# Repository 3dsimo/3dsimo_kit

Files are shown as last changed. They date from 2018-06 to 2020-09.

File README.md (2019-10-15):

# 3Dsimo KIT information

## Watch our PROMO video for 3Dsimo KIT 2 product

Visit us at [3D simo pages](https://3dsimo.com/) for more information

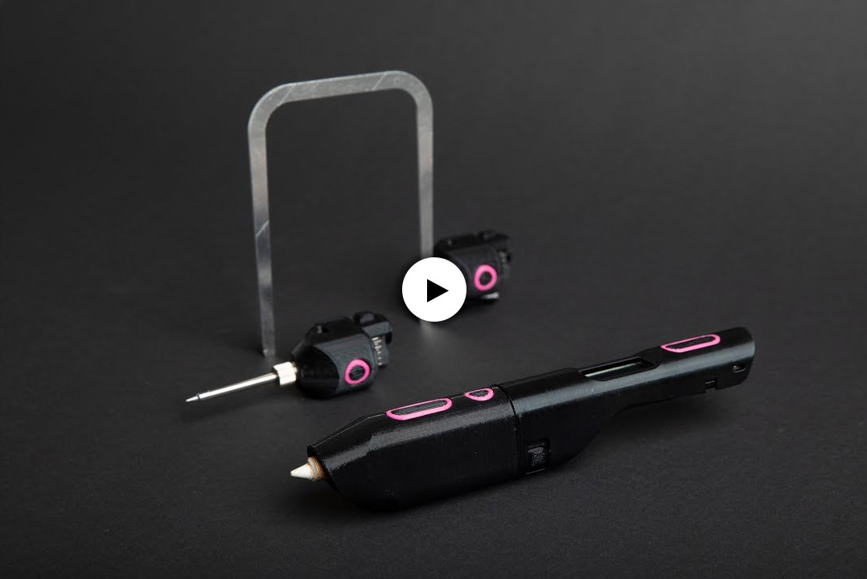
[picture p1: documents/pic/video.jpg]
(https://www.youtube.com/watch?v=d5TUmM0rqjs)


## [3D printed parts](documents/3Dprint.md)
This section includes information about all 3D printed plastic parts. Folder [3Dmodels](3Dmodels) includes all parts in STP and STL formats for both version of 3Dsimo KIT. You can download it and edited it as you want. If your models will be awsome, we can publish them here.

## [Hardware for 3Dsimo KIT](documents/Hardware.md)
Electronics device is an essential part of the 3Dsimo KIT. Main board is a "heart" of the device and manage all functions such as heating, identification or extrusion. 

## [Firmware for 3Dsimo KIT](documents/Firmware.md)
Microcontroller requries a program which can run the device. 3Dsimo KIT has code written in C/C++ language in [Arduino IDE](https://www.arduino.cc/) and it is easy to edit.

## [Arduino nano](documents/ArduinoNano.md)
Information about Arduino Nano like development board. 

## [Manuals](documents/Manual.md)
Manual for device operations and how to edit your Arduino Nano like development kit for 3Dsimo KIT. 

<!--
## [Material profiles](documents/MaterialProfiles.md)
-->

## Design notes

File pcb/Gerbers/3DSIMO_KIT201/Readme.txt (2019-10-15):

I order Rigid Board with these parameters and files:

Name:               3DSIMO_KIT201
Customer:           3DSimo

PCB Parameters:
Type:               Rigid FR4
Number of layers:   2 rigid 
Final thickness:    1.6 mm
Copper thickness:   35um
Coating:            HAL Free
Soldermask TOP:		Black
Soldermask BOT:		Black
Silkscreen TOP:		White
Silkscreen Bottom:  White
Dimensions:			17 x 85 mm

Input Files:
bot.gbr             Copper - BOTTOM side
top.gbr             Copper - TOP side   
mill.gbr            Milling of PCB
plt.gbr             Silkscreen - TOP
plb.gbr             Silkscreen - BOTTOM
smb.gbr             Solder mask - BOTTOM side
smt.gbr             Solder mask - TOP side
npth.exc            Non plated drills
pth.exc             Plated drills
paste_top.gbr       SMD stencil - TOP

Copper order:
TOP
BOTTOM

Output testing:
Electrical testing: YES

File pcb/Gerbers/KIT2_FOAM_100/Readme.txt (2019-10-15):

I order Rigid Board with these parameters and files:

Name:               KIT2_FOAM_100
Customer:           3DSimo

PCB Parameters:
Type:               FR4
Number of layers:   2 
Final thickness:    1.6 mm
Copper thickness:   35um
Coating:            Immersion Au
Soldermask TOP:		White
Soldermask BOT:		White
Silkscreen TOP:		None
Silkscreen Bottom:  None
Board dimensions:	26.30 x 17.15 mm

Input Files:
bot.gbr             Copper - BOTTOM side 
top.gbr             Copper - TOP side    
mill.gbr            Milling of PCB
smb.gbr             Solder mask - BOTTOM side
smt.gbr             Solder mask - TOP side
npth.exc            Non plated drills
pth.exc             Plated drills  
paste_top.gbr		Stencil layer TOP

Copper order:
TOP
BOTTOM 

Output testing:
Electrical testing: YES

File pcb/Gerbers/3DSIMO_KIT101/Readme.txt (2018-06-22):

I order Rigid Board with these parameters and files:

Name:               3DSIMO_KIT101
Customer:           3DSimo

PCB Parameters:
Type:               Rigid FR4
Number of layers:   2 rigid 
Final thickness:    1.6 mm
Copper thickness:   35um
Coating:            HAL Free

Input Files:
bot.gbr             Copper - BOTTOM side
top.gbr             Copper - TOP side   
mill.gbr            Milling of PCB
plb.gbr             Silkscreen - BOTTOM
plt.gbr             Silkscreen - TOP
smb.gbr             Solder mask - BOTTOM side
smt.gbr             Solder mask - TOP side
npth.exc            Non plated drills
pth.exc             Plated drills

Copper order:
TOP
BOTTOM

Output testing:
Electrical testing: YES

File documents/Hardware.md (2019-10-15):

# Hardware for 3Dsimo KIT 2

3Dsimo KIT 2 is based on standard Arduino Nano platform with modified layout designed especially for 3D pen with interchangable extensions. Its simplified design lead to smaller footprint and thus smaller and more ergonomical design of the whole device. 

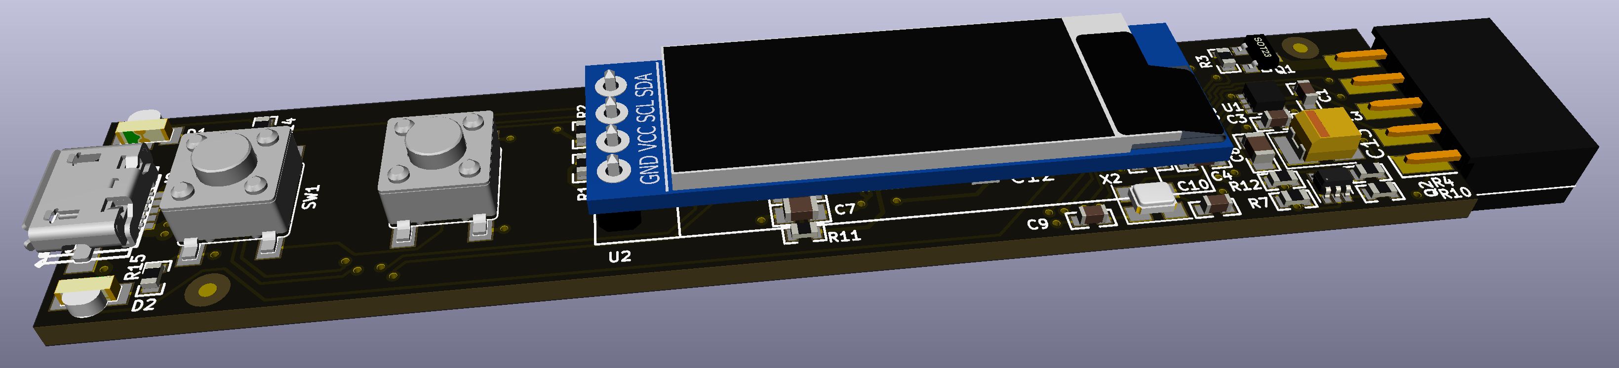
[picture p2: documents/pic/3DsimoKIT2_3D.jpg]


### Power
The pen runs at 5V power through micro USB connector which is possible to use as a programming interface as well. The device requires power adapter with at least 2A and 5V. 

### Display
OLED display based on SSD1306 driver is connected through an TWI interface to the microcontroller. There are two external pull-ups resistor which are making logical 1 for the TWI bus and no additional components are required.

### Programming interface
The microcontroller is possible to reprogram through the USB and USB<>UART converter. The layout is similar to standard Arduino Nano programming interface, but chosen converter is different - CP2102N. Program is written in C/C++ language in Arduino IDE. More information about programming you can find in [Firmware chapter](Firmware.md).

### Layout
3Dsimo KIT 2 contains 4 boards, where one is main board with MCU and three boards are used for interchangable extensions. All boards are designed in Open-source program [KiCAD](http://kicad-pcb.org/) in the recent version 5.1.4. 3D models are mainly taken from KiCADs repositories, but several were drawn or taken from the manufacturer and they are not included in KiCADs github. You can find them in folder with all [3D models](../pcb/Documents/3D) used for 3DSimo KIT.

### Temperature measurement
3Dsimo KIT2 is equipped with two ranges thermal measurement, one for PCL materials (temperatures in range from 30°C to 120°C) and the second one for other plastics material such as ABS, PLA, etc. (from 180°C to 300°C). These two ranges provides unlimited possibilities in different material usage. 

### Schematics and Assembling
Schematics of the 3Dsimo KIT 2 is possible to download at [following link](../pcb/Documents/3DsimoKit201_Schematics.pdf)

Assembling and components placement can be downloaded at [following link](../pcb/Documents/3DsimoKit201_AssemblyTop.pdf)

# Hardware for 3Dsimo Kit
3Dsimo KIT is developed on Arduino Nano like development board with additional interface board containing motor driver and OLED display. 

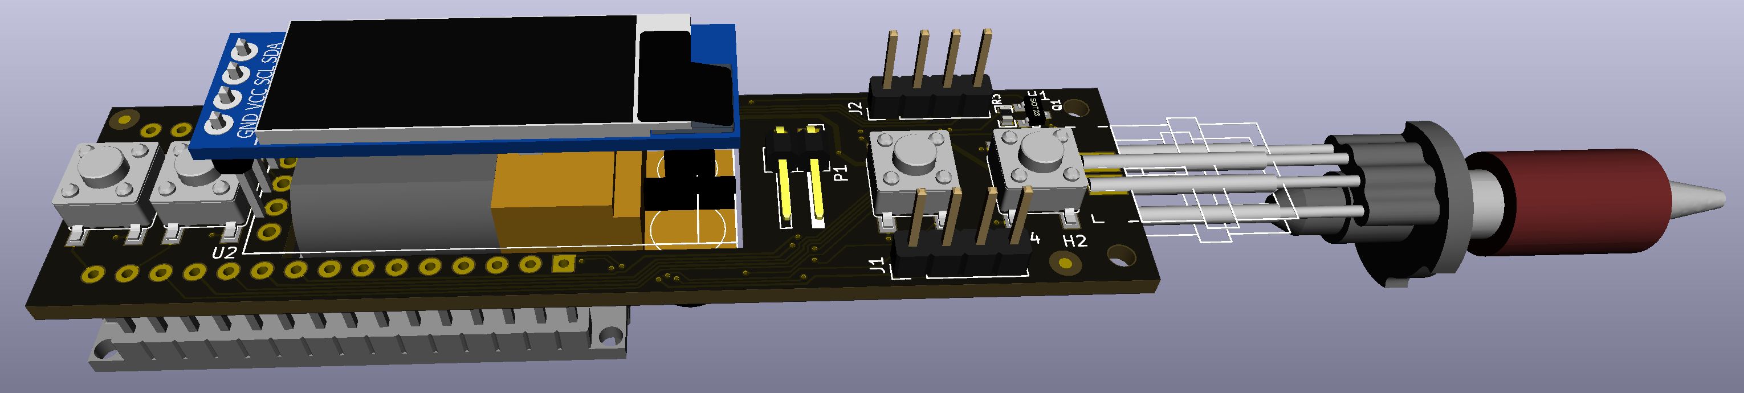
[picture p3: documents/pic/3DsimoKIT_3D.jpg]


### Power
The pen runs at 5V power through mini USB connector located on Arduino Nano like board. The development board requires one modification, replace input protection diode for shortcut. 3Dsimo KIT requires power adapter with at least 2A and 5V. 

### Display
OLED display based on SSD1306 driver is connected through an TWI interface and additional board to the microcontroller. There are two external pull-ups resistor which are making logical 1 for the TWI bus and no additional components are required.

### Programming interface
The microcontroller is possible to reprogram through the mini USB connector placed directly on the Arduino Nano like development kit. Program is written in C/C++ language in Arduino IDE. More information about programming you can find in [Firmware chapter](Firmware.md).

### Layout
3Dsimo KIT contains one interface board, which is used for connecting display, buttons, motor driver and etc. with MCU. The board is designed in Open-source program [KiCAD](http://kicad-pcb.org/). 3D models are mainly taken from KiCADs repositories, but several were drawn or taken from the manufacturer and they are not included in KiCADs github. You can find them in folder with all [3D models](../pcb/Documents/3D) used for 3DSimo KIT.

### Temperature measurement
3Dsimo KIT is equipped with only one range for melting common plastics for 3D printers such as ABS, PLA, etc. and its range is from 180°C to 300°C. 

### Schematics and Assembling
Schematics of the 3Dsimo KIT 2 is possible to download at [following link](../pcb/Documents/3DsimoKit101_Schematics.pdf)

Assembling and components placement can be downloaded at the following links [TOP](../pcb/Documents/3DsimoKit101_AssemblyTop.pdf) and [BOTTOM](../pcb/Documents/3DsimoKit101_AssemblyBottom.pdf)

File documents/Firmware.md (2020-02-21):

# Firmware for 3Dsimo KIT
If you want to learn how the pen works or you want to add your own material profiles, or you want to make some changes and tweaks, you are on the right address. The code is fully available and commented so you don't have trouble finding your way around. For both versions of the 3Dsimo KIT Firmwares are inside folders [FW](../FW). 

Microcontroller is programmed in C/C++ language in the editor [Arduino IDE](https://www.arduino.cc/). 

Main code is divided into several files, where every have different purpose. Following listing explains their purpose:
 - **config.h** is for setting pins and general settings of the board 
 - **accessories.c/.h** contains functions for every extension
 - **NanodeUNIO.c/.h** is library for one wire UNI/O protocol, it is used for identification the extensions

Before you start to program or edit the code, it is required to download some libraries listed below.

## Libraries to download
Code for 3Dsimo KIT requires following two libraries which have to be downloaded. 
 - **EveryTimer** by *Alessio Leoncini*
 - **ssd1306** by *Alexey Dynda*
 
Both libraries you can download directly from Arduino IDE according to following image (Sketch -> Include Library -> Manage Libraries ...)

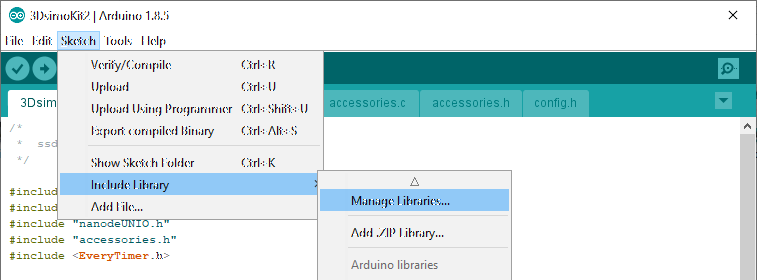
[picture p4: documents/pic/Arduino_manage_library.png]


## Setting up Arduino IDE
### Board
Both version of the 3Dsimo KIT requires to choose development kit Arduino Nano board (Tools -> Board: ... -> Arduino Nano)

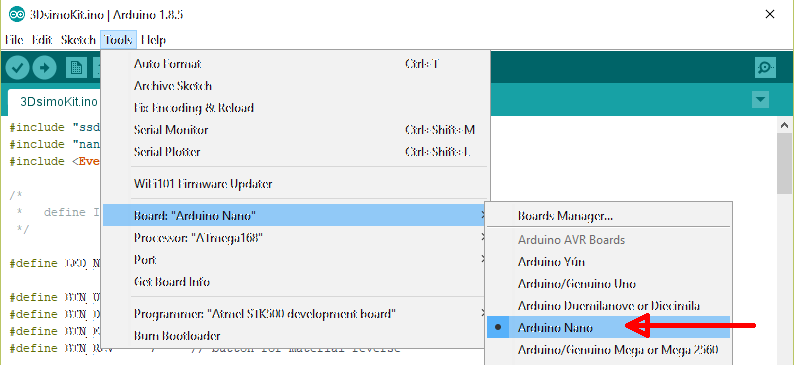
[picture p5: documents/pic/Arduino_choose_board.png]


### COM port
Select port where is connected your development kit (Tools -> Port -> COMxx). In the image, there is selected COM3, but your board can be connected to a different one.

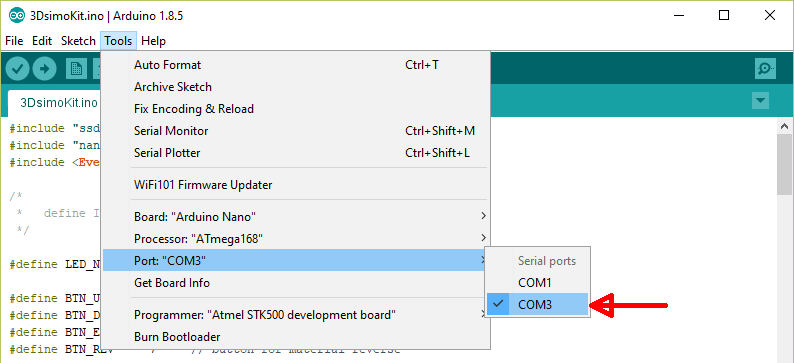
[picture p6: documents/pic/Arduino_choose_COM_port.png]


### Processor
**3Dsimo KIT** can use both types of microcontroller, you have to check it which one you have. The most probably version is **ATmega168**. 

The **3Dsimo KIT 2** is using **ATmega328P**. 

Please be sure, you are using the right version of the bootloader. Arduino released a new version of Arduino IDE, where updated bootloader for Arduino NANO boards. In this case, used setting with a processor called **ATmega328P (old bootloader)**. 

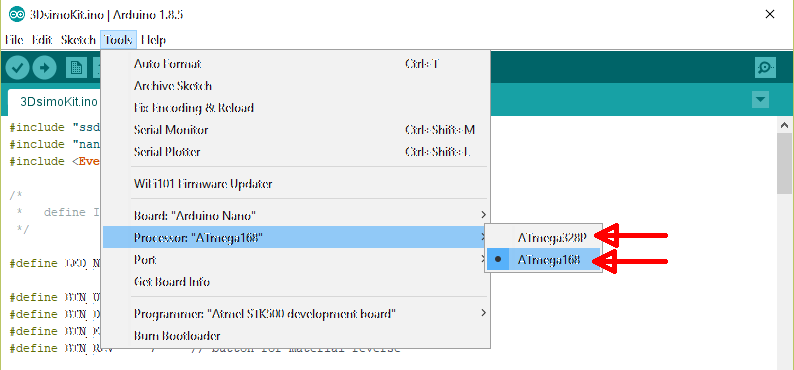
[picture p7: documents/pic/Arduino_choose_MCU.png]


## Compiling and uploading code

When you finish editing your code, it is possible to verify it by the first button "Verify" (1) and in case of no errors upload it to the microcontroller by the second (2) button "Upload". Uploading progress bar will indicate the process of the upload. When code is successfully uploaded into microcontroller, the status will be following: "Done uploading".

In case of error, the editor will not permit to upload the code into microcontroller.

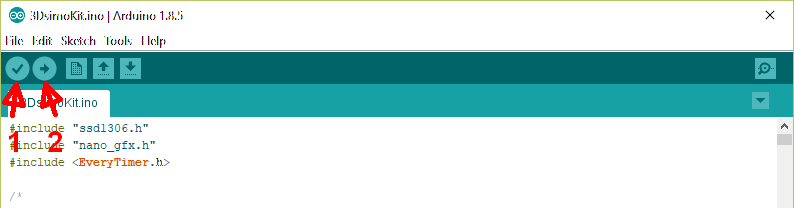
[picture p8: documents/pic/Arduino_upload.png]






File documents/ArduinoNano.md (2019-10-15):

# Arduino Nano development kit
3Dsimo KIT is based on very popular Arduino Nano. It is very likely that you already come across it but in case you haven't yet here are some things you might find useful.

The first version of 3Dsimo KIT requires standard Arduino Nano board, but it is necessary to perform one small improvement (development boards supplied by 3Dsimo have this improvement performed). It is necessary to replace input protection diode which limits input power to the board. The 3D extension requires more than 1.5A and this diode limit the current to approx 500mA. It depends on type. Replacement is illustrated in the following image in red circle. There is replaced diode by 0R resistor.

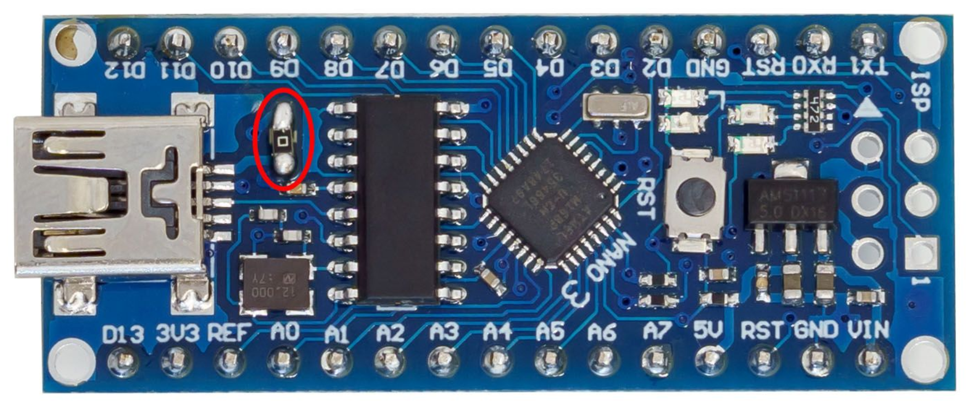
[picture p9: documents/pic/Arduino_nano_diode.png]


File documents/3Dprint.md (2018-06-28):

# 3D print
Plastic parts of 3Dsimo KIT are printed on FDM printers and can be easily swapped. We intend to add new parts and new designs all the time. All 3D models are of course available, so you can modify them as you please. IF you have an interesting model don't hesitate to share it with us.

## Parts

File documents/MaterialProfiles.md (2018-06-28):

# Material profiles
3Dsimo KIT already contains profiles for ABS and PLA of the box, but thanks to its nature, it can handle other materials easily as well. You can even add them yourself by changing our available code and adding your own material profiles.

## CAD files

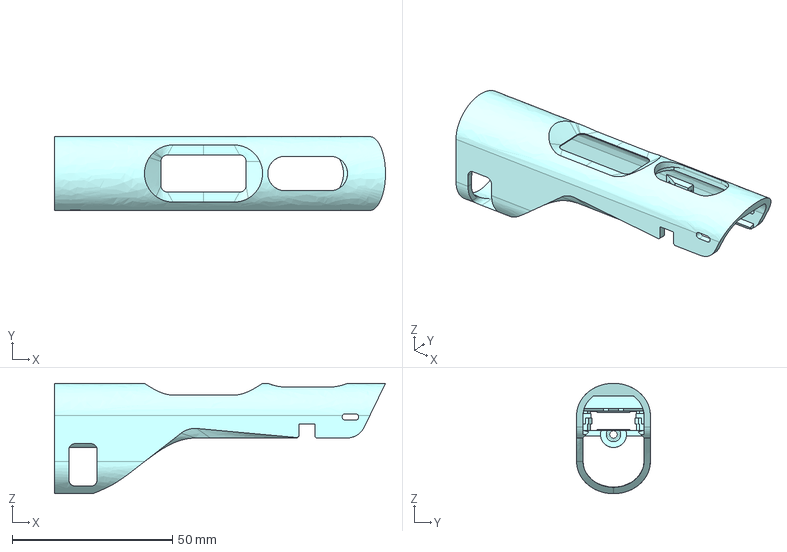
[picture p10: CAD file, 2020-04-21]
3Dmodels/3Dsimo KIT2/Newer/STP/MAIN BODY.step
103.1 x 23.0 x 34.4 mm

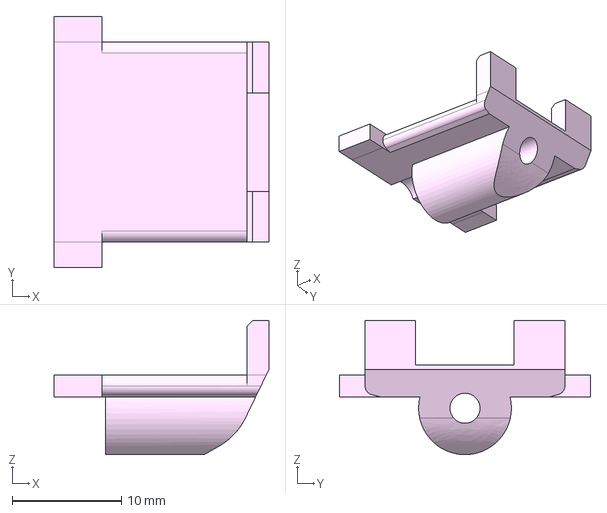
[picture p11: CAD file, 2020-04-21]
3Dmodels/3Dsimo KIT2/Newer/STP/MAIN_PCB_FASTENING v1.step
19.7 x 23.0 x 12.3 mm

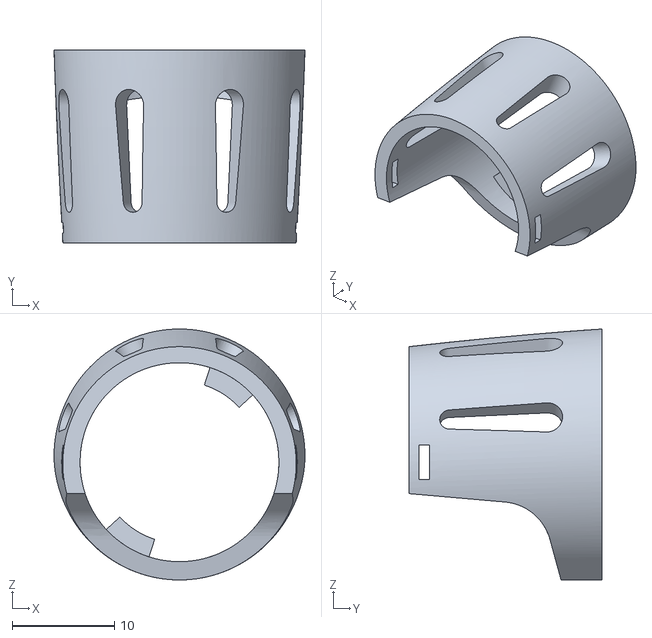
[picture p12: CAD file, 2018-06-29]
3Dmodels/3Dsimo KIT/original/STL/Front_Ring_Alt_1.stl
24.5 x 18.8 x 24.5

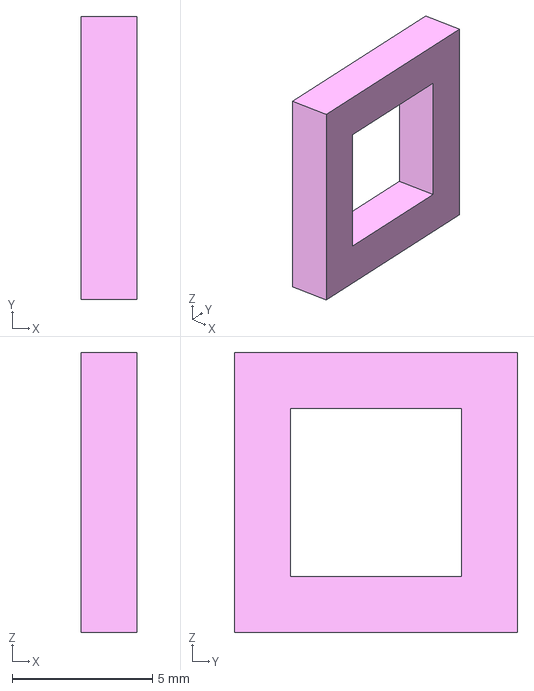
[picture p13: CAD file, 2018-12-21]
3Dmodels/3Dsimo KIT/original/STP/Lock_side_2x.stp
2.00 x 10.1 x 10.0 mm

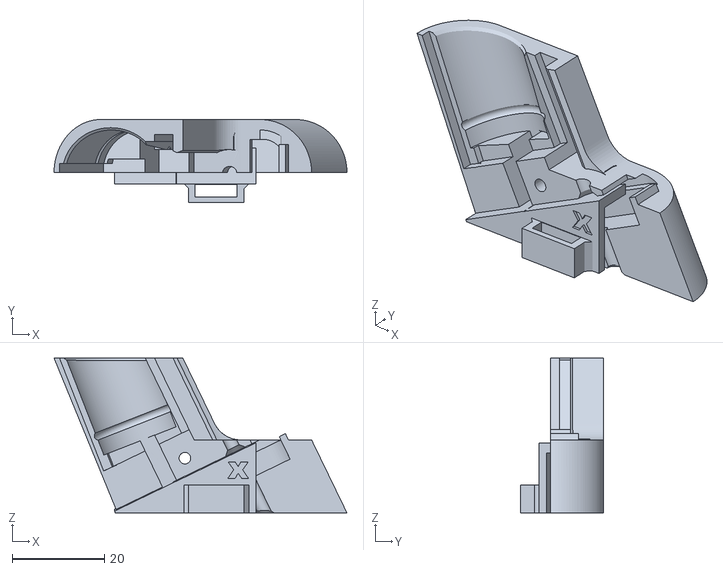
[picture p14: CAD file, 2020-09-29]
3Dmodels/3Dsimo KIT2/Battery_adaptor/modeled supports/BAT_LEFT_SUPPORTS.stl
63.4 x 17.9 x 33.5

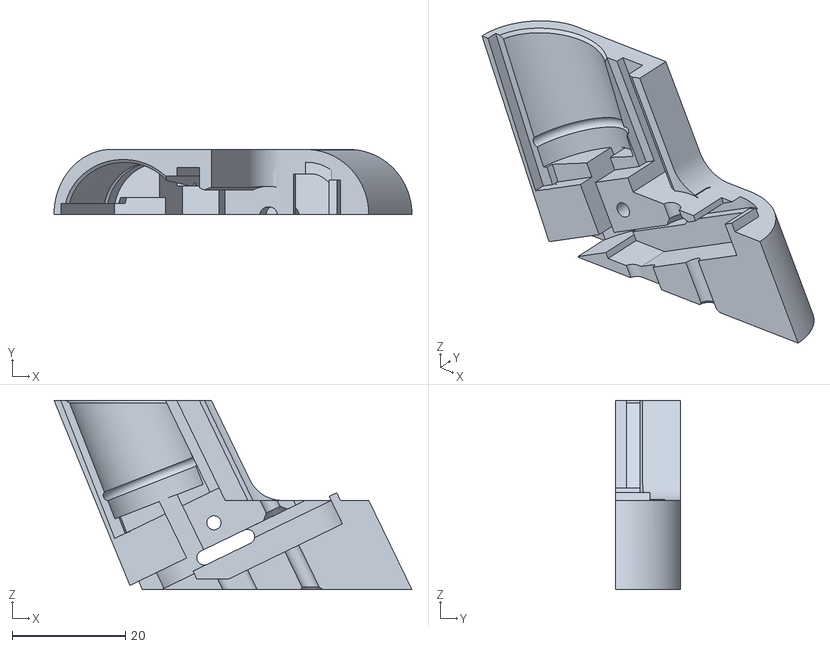
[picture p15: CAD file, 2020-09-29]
3Dmodels/3Dsimo KIT2/Battery_adaptor/original/BAT_LEFT.stl
63.4 x 11.5 x 33.5

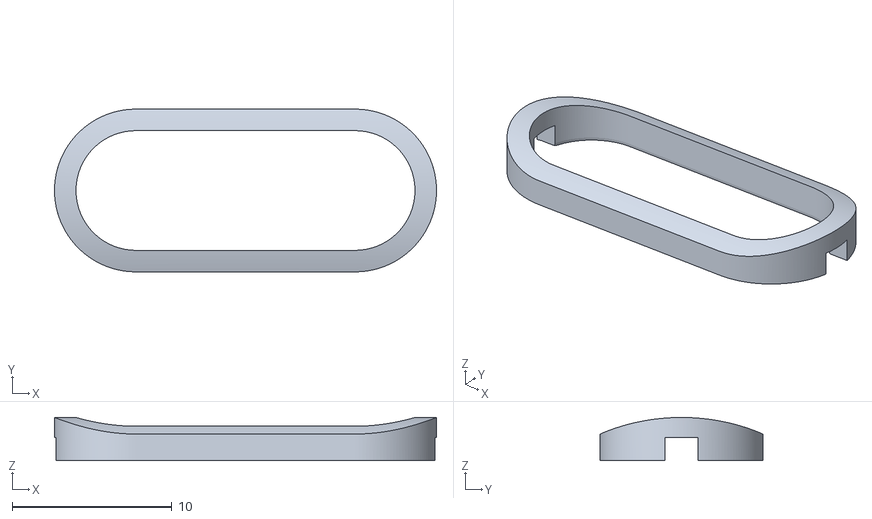
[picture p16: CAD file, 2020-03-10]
3Dmodels/3Dsimo KIT2/Newer/STL/DOUBLE BUTTON RING.stl
23.9 x 10.2 x 2.70

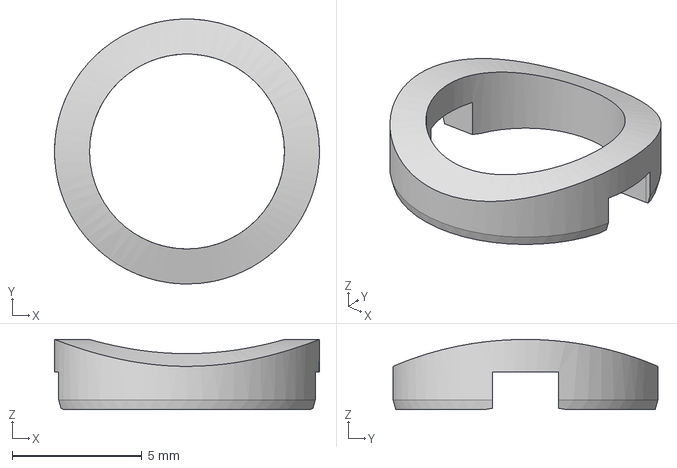
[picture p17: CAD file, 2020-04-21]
3Dmodels/3Dsimo KIT2/Newer/STP/SINGLE_BUTTON_RING v1.step
10.2 x 10.2 x 2.70 mm

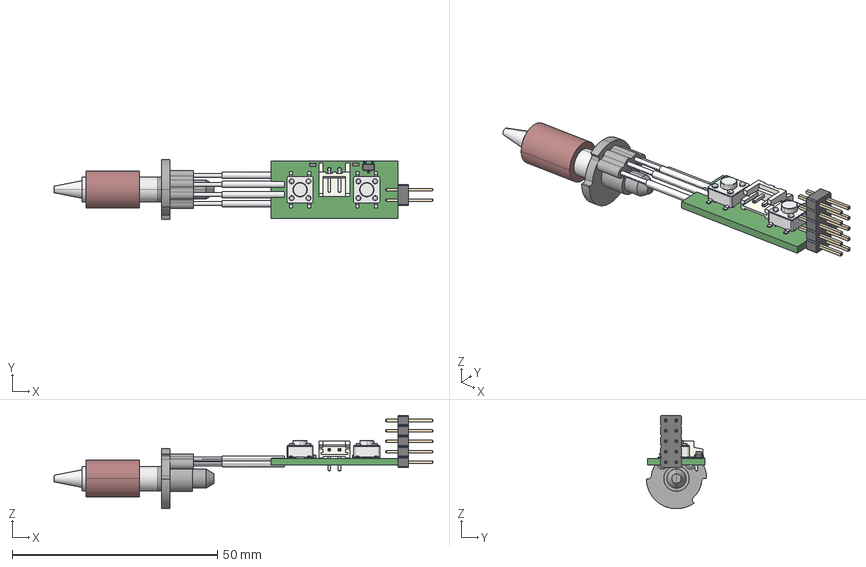
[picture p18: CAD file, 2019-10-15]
pcb/Documents/3D/KIT2_3D_extension100.step
92.4 x 14.7 x 22.8 mm

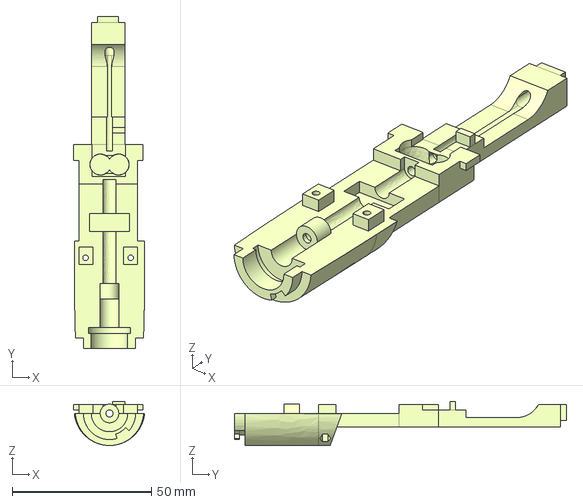
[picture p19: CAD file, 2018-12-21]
3Dmodels/3Dsimo KIT/original/STP/Central_bottom.stp
25.6 x 119.1 x 15.8 mm

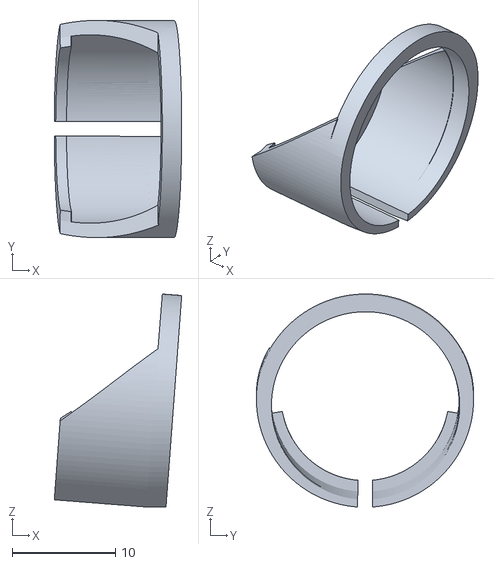
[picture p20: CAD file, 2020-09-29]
3Dmodels/3Dsimo KIT2/Battery_adaptor/original/BAT_RING.stl
12.3 x 21.0 x 20.6

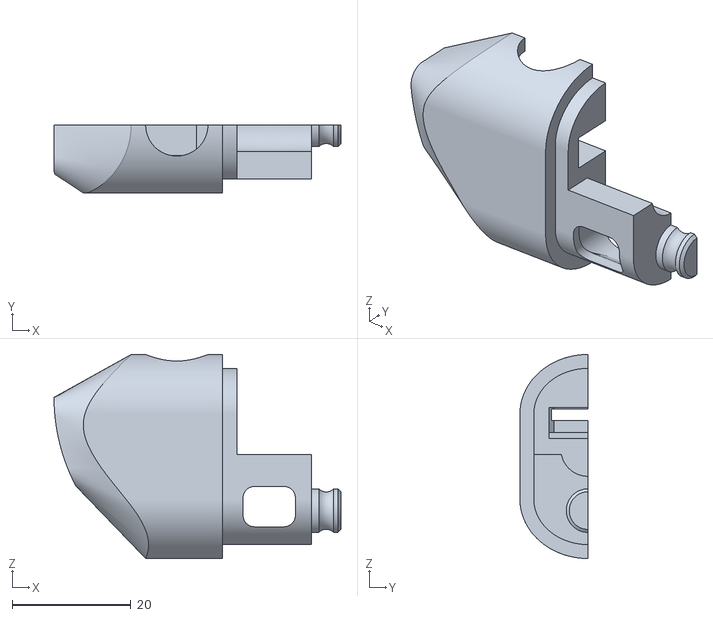
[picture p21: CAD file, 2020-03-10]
3Dmodels/3Dsimo KIT2/Newer/STL/FOAM LEFT.stl
48.4 x 11.5 x 34.4

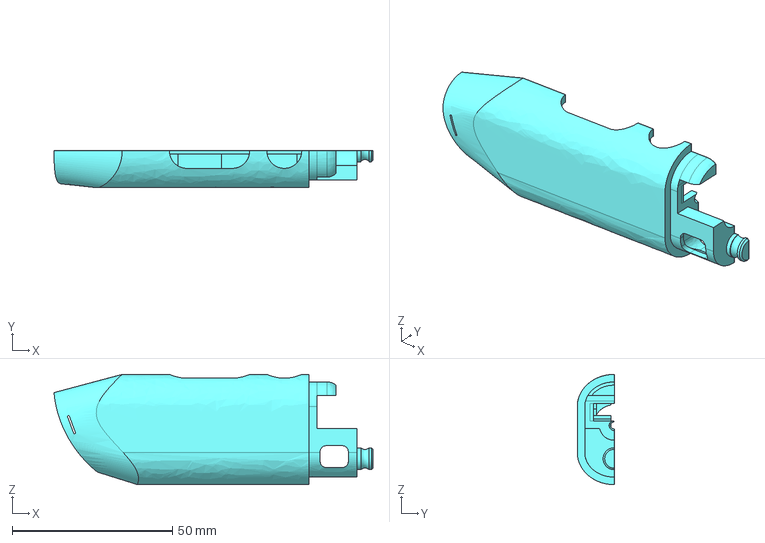
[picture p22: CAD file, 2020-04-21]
3Dmodels/3Dsimo KIT2/Newer/STP/3D_DRAW_R.step
99.6 x 11.7 x 34.4 mm

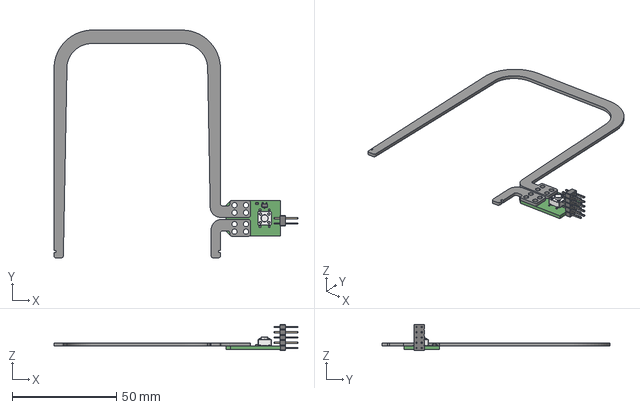
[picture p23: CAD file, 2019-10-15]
pcb/Documents/3D/KIT2_foam_cutting100.step
117.3 x 109.5 x 12.7 mm

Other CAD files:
3Dmodels/3Dsimo KIT2/Battery_adaptor/modeled supports/BAT_RIGHT_SUPPORTS.stl
3Dmodels/3Dsimo KIT/original/STP/Central_top.stp
3Dmodels/3Dsimo KIT2/Battery_adaptor/modeled supports/BAT_RING_SUPPORTS.stl
3Dmodels/3Dsimo KIT2/Battery_adaptor/original/BAT_RIGHT.stl
3Dmodels/3Dsimo KIT/original/STL/Back_Top.stl
3Dmodels/3Dsimo KIT/original/STL/Central_Bottom.stl
3Dmodels/3Dsimo KIT/original/STL/Central_Top.stl
3Dmodels/3Dsimo KIT/original/STL/Front_Ring.stl
3Dmodels/3Dsimo KIT/original/STL/Front_Ring_Alt_2.stl
3Dmodels/3Dsimo KIT/original/STL/Lock_Back.stl
3Dmodels/3Dsimo KIT/original/STL/Lock_Side_2x.stl
3Dmodels/3Dsimo KIT/original/STL/Tube_Holder.stl
3Dmodels/3Dsimo KIT/original/STP/Back_top.stp
3Dmodels/3Dsimo KIT/original/STP/Front_ring.stp
3Dmodels/3Dsimo KIT/original/STP/Front_ring_Alt_2.stp
3Dmodels/3Dsimo KIT/original/STP/Lock_back.stp
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

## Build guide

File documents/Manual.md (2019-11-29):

# 3Dsimo KIT manuals
Want to learn more about 3Dsimo KIT? Everything you should know about it can be find here. Steps how to assemble the pen, how to power it, how to program it, what types of filament to use.

## English Manual

[Assembly Manual 3Dsimo KIT](pdf/manualEN.pdf)

[Assembly Manual 3Dsimo KIT2](pdf/KIT_2_4in1_en.pdf)

## Czech Manual

[Assembly Manual 3Dsimo KIT](pdf/manualCZ.pdf)

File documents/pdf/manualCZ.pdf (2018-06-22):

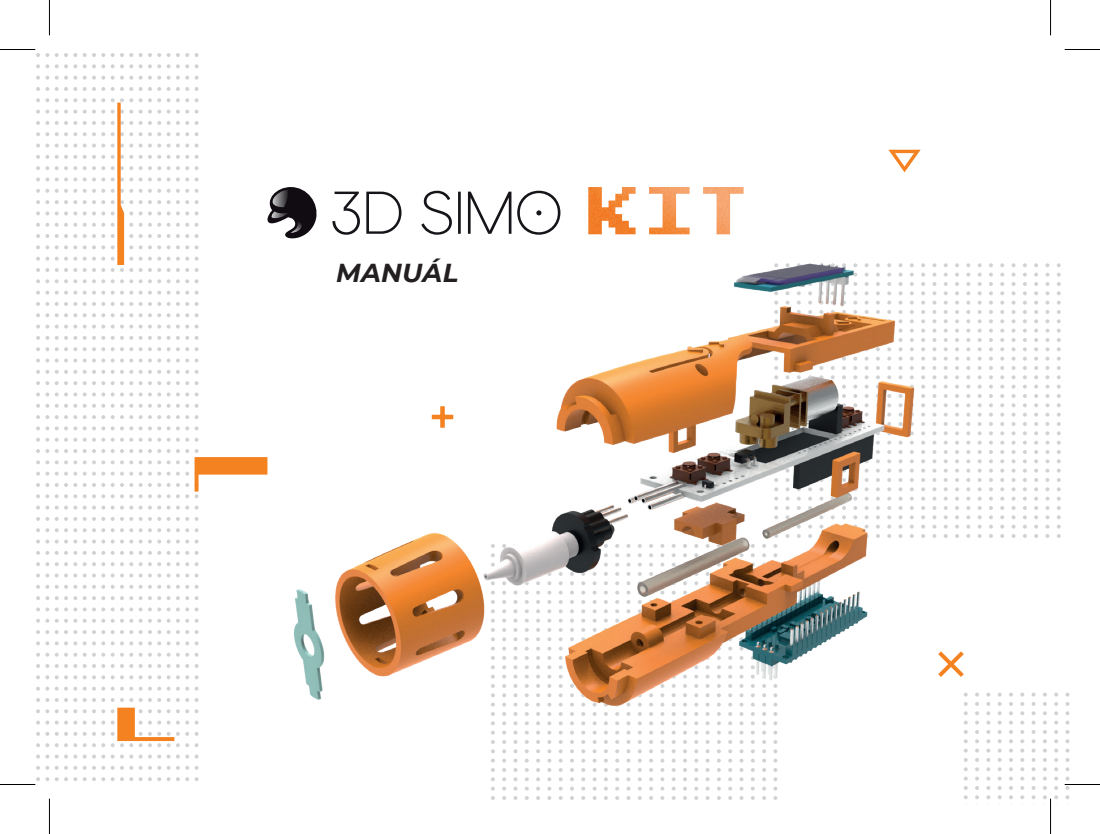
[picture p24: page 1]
MANUÁL

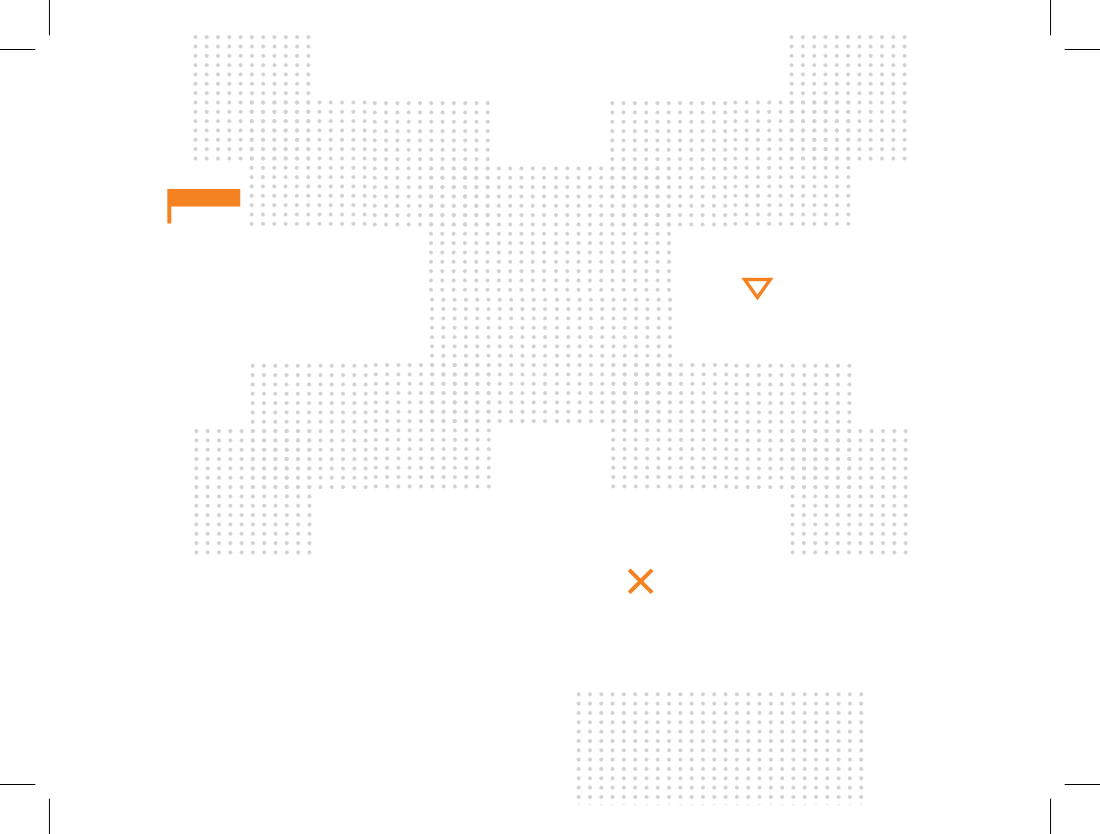
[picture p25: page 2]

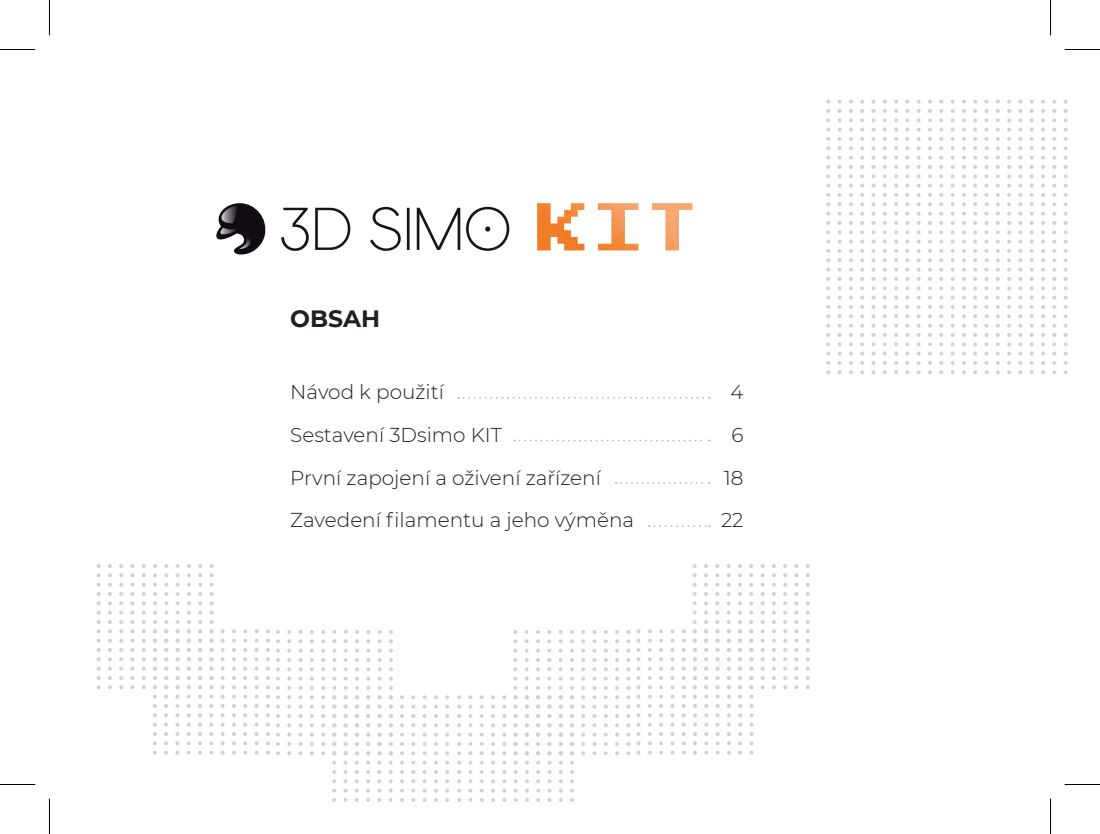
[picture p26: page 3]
OBSAH

Návod k použití
Sestavení 3Dsimo KIT
První zapojení a oživení zařízení
Zavedení filamentu a jeho výměna

ٱ Do rukou se vám dostala stavebnice multimateriálového 3D pera. ٱ Tato stavebnice je kompletně open source a k ovládání využíváme Arduino Nano.
ٱ Časová náročnost sestavení: 15 – 30 min.
ٱ Před zahájením stavby si rozložte na stůl všechny díly a zkontrolujte, jestli máte vše ze seznamu.
ٱ V balení naleznete náhradní díly malých komponentů (šroubky, matičky, teflonové trubičky).
ٱ Na spodku krabičky máte přiloženo 5 m kreslícího filamentu ABS. ٱ Můžete používat stejné filamenty které využívají 3D tiskárny.
ٱ Filament musí mít průměr 1,75 mm.

# NÁVOD K POUŽITÍ

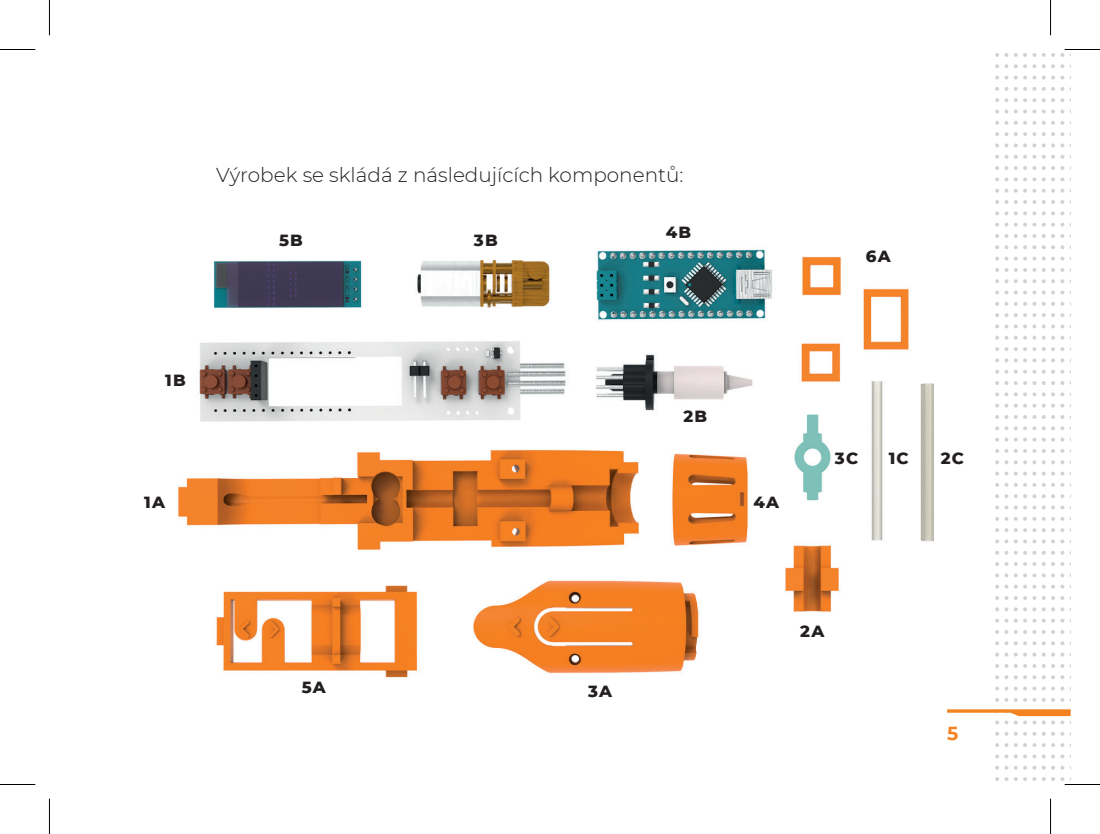
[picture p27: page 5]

Výrobek se skládá z následujících komponentů:

# SESTAVENÍ 3DSIMO KIT

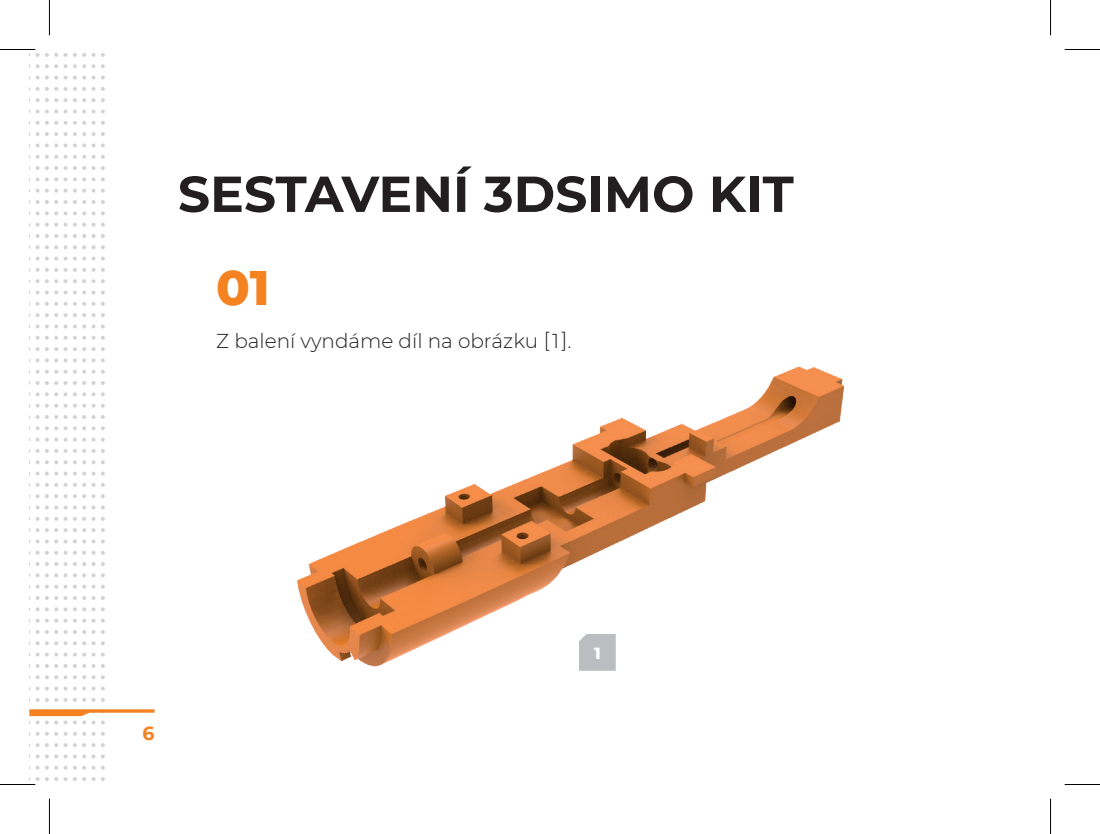
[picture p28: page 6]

Z balení vyndáme díl na obrázku [1].

Do připraveného dílu vložíme teflonové trubičky. Nejdříve trubičku o průměru 3 mm (1C) vložíme do zadní části. Tato trubička zajištuje vedení struny k extruderu (motor s podávacím kolečkem). Následně vložíte do přední části trubičku o průměru 4 mm (2C). Pokud jsou trubičky příliš dlouhé, zkraťte je nožem.

02

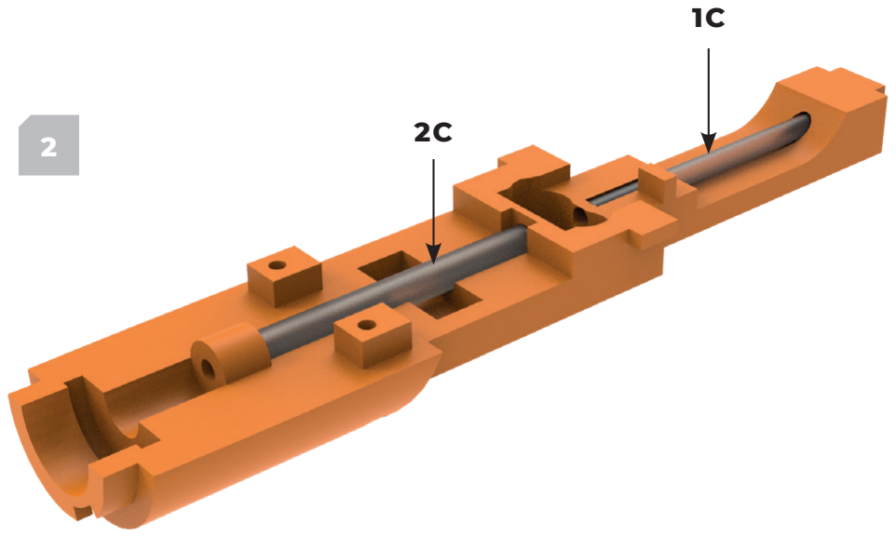
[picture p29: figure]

Díl (2A) vložíme na místo znázorněné na obrázku [3]. Tento díl slouží k zajištění teflonové trubičky. V tento moment je čas vzít kousek filamentu (před zasunutím narovnejte). Vložte do trubičky a otestujte, jestli filament v pořádku prochází z jedné strany na druhou. Pokud filament neprochází plynule je pravděpodobně trubička ohnutá. Po narovnání bude vše v pořádku.

03

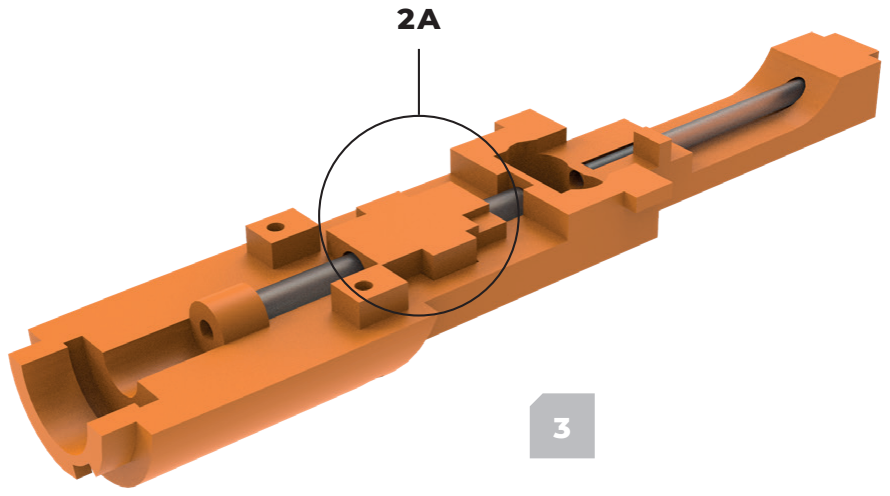
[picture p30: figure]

04

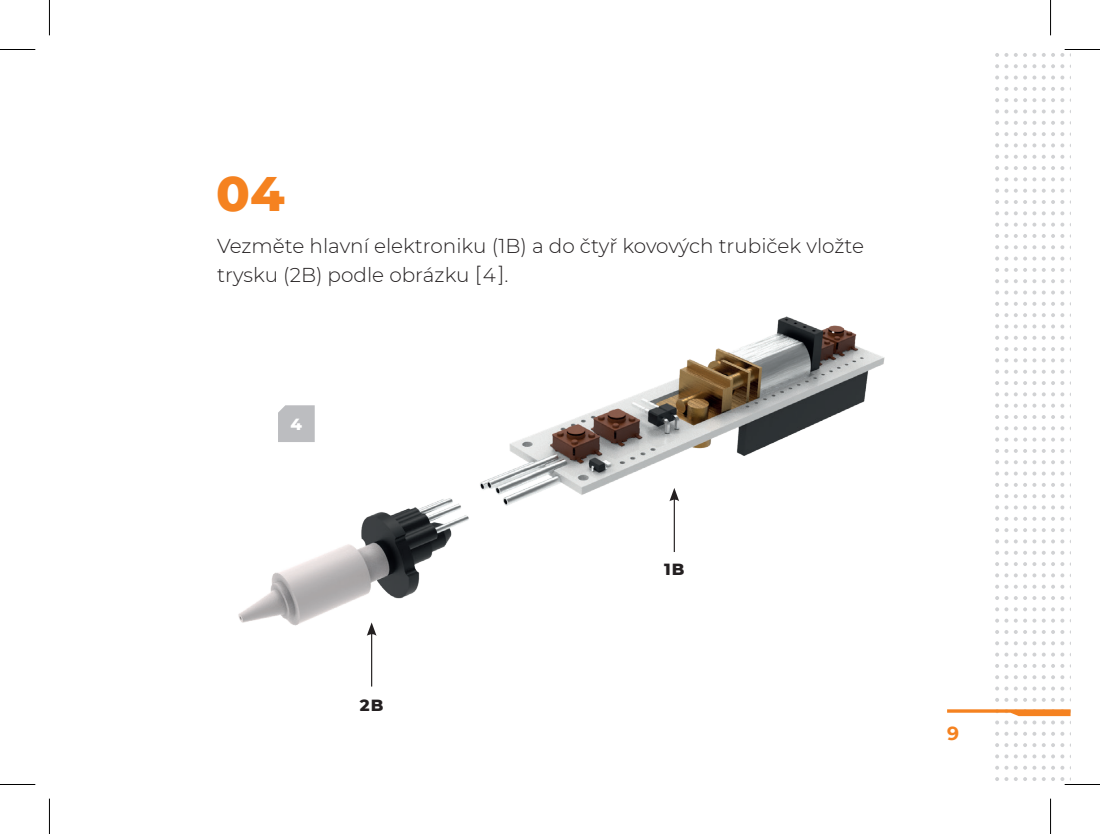
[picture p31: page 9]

Vezměte hlavní elektroniku (1B) a do čtyř kovových trubiček vložte
trysku (2B) podle obrázku [4].

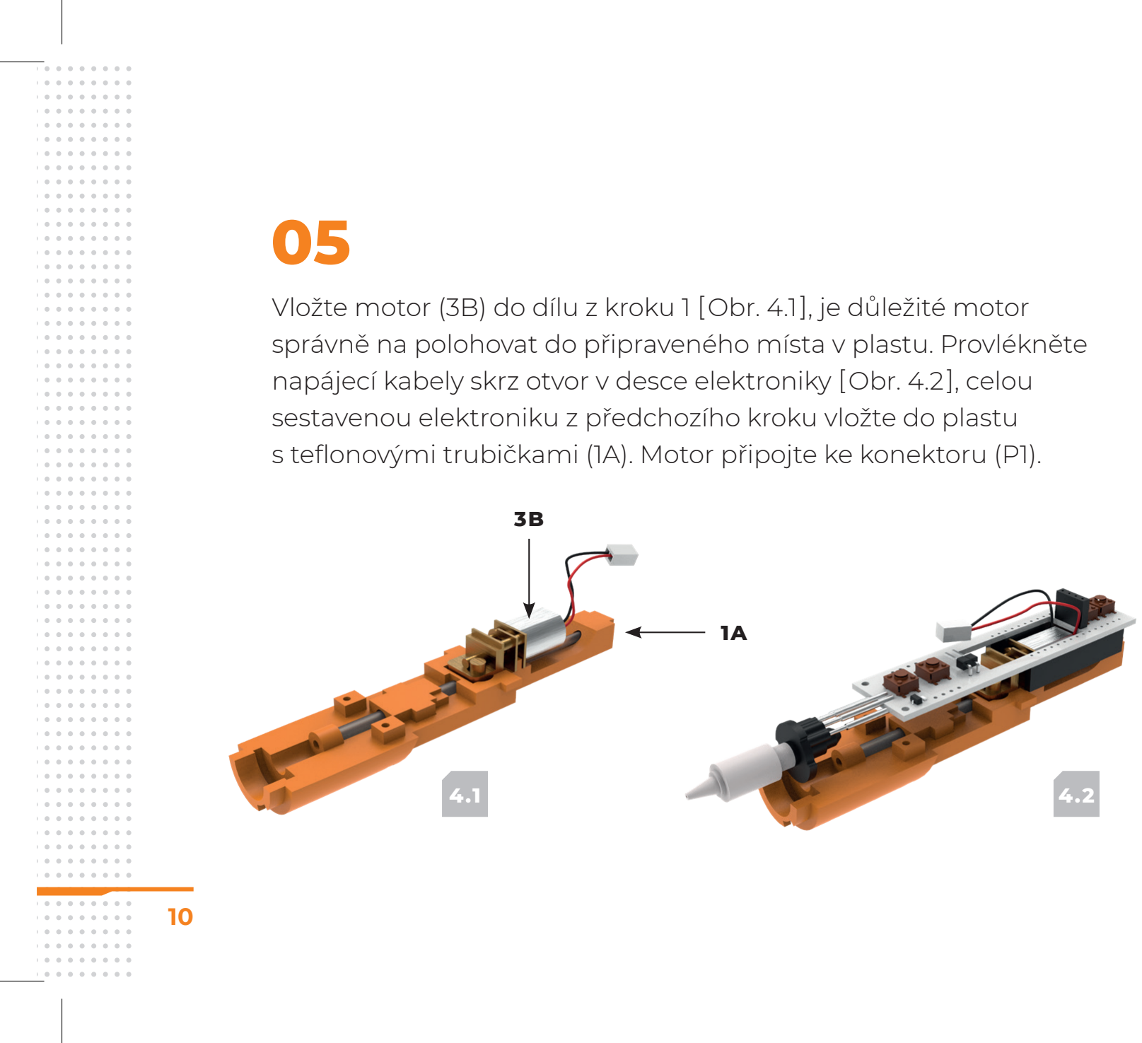
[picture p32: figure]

Vložte motor (3B) do dílu z kroku 1 [Obr. 4.1], je důležité motor správně na polohovat do připraveného místa v plastu. Provlékněte napájecí kabely skrz otvor v desce elektroniky [Obr. 4.2], celou sestavenou elektroniku z předchozího kroku vložte do plastu
s teflonovými trubičkami (1A). Motor připojte ke konektoru (P1).

06

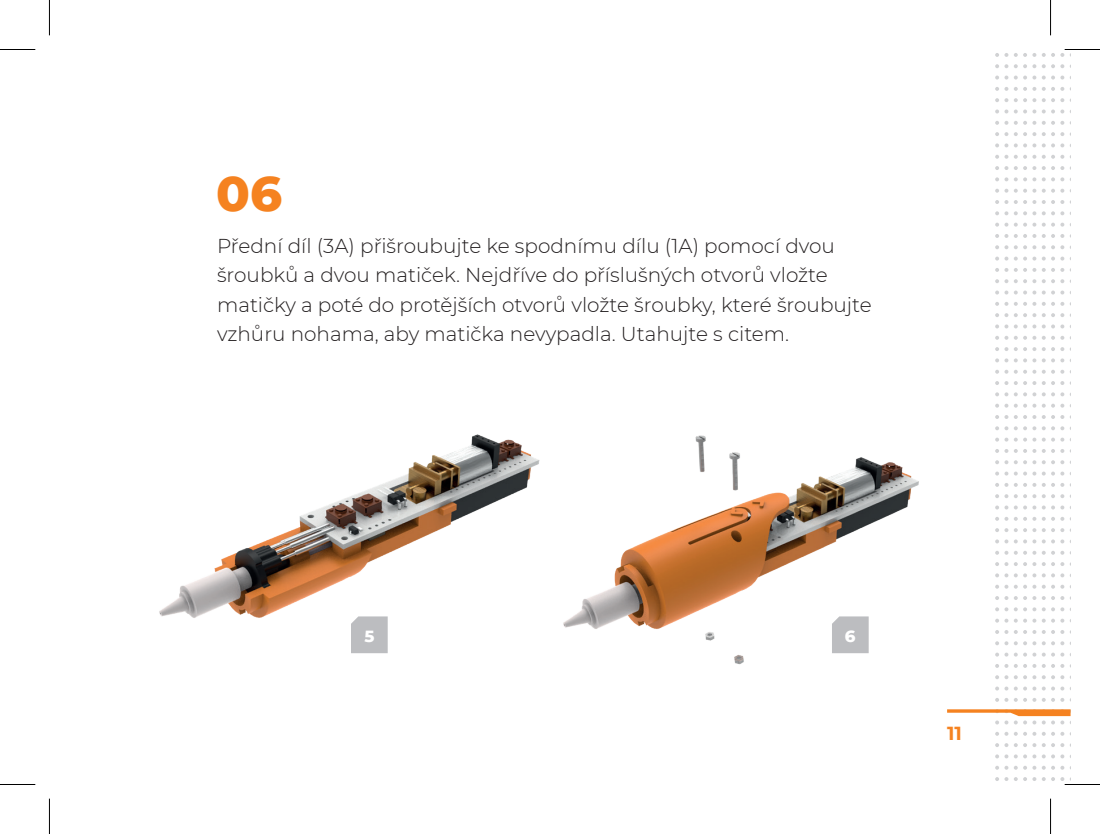
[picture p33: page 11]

Přední díl (3A) přišroubujte ke spodnímu dílu (1A) pomocí dvou
šroubků a dvou matiček. Nejdříve do příslušných otvorů vložte
matičky a poté do protějších otvorů vložte šroubky, které šroubujte
vzhůru nohama, aby matička nevypadla. Utahujte s citem.

07

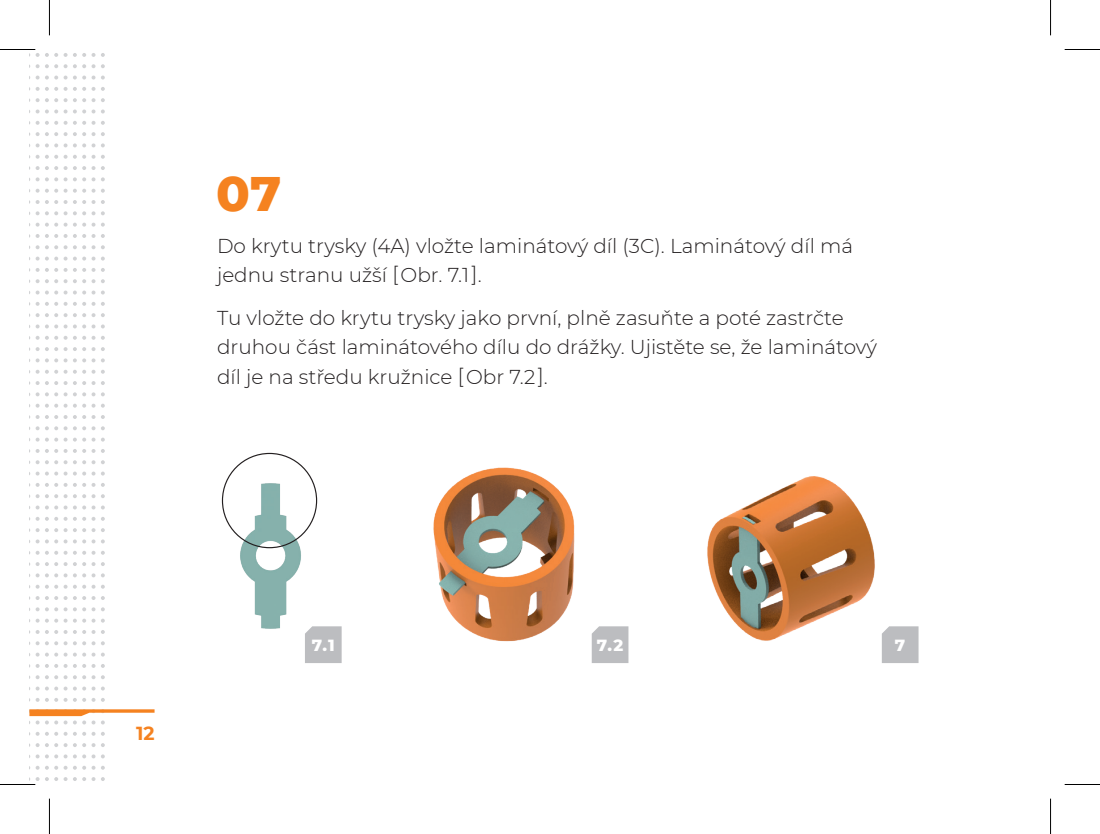
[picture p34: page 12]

Do krytu trysky (4A) vložte laminátový díl (3C). Laminátový díl má
jednu stranu užší [Obr. 7.1].
Tu vložte do krytu trysky jako první, plně zasuňte a poté zastrčte
druhou část laminátového dílu do drážky. Ujistěte se, že laminátový
díl je na středu kružnice [Obr 7.2].

08

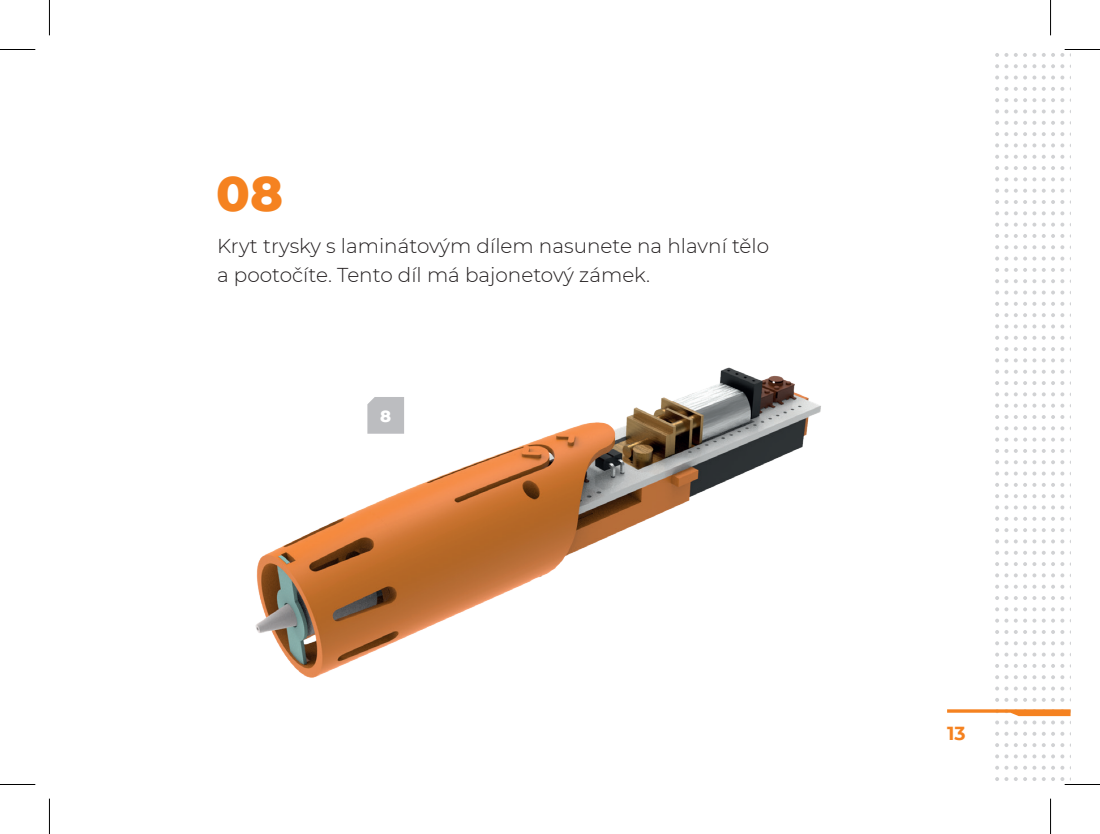
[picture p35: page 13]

Kryt trysky s laminátovým dílem nasunete na hlavní tělo
a pootočíte. Tento díl má bajonetový zámek.

09

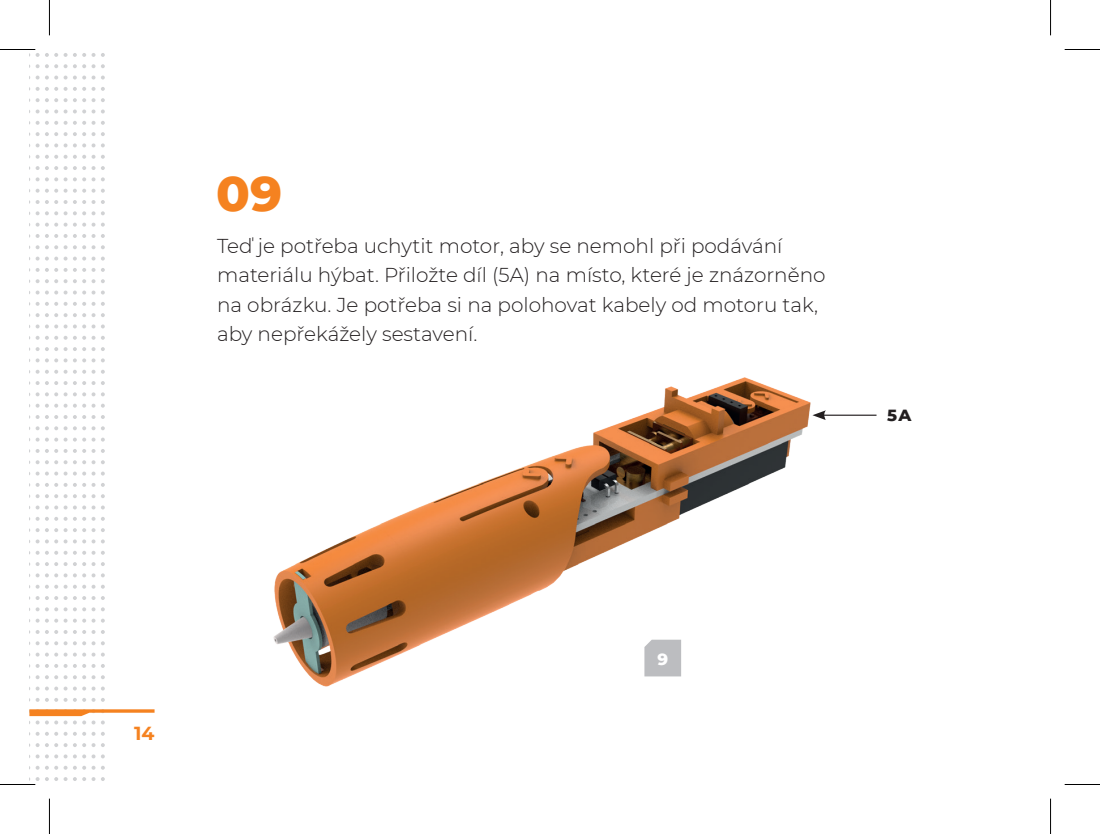
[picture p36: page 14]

Teď je potřeba uchytit motor, aby se nemohl při podávání
materiálu hýbat. Přiložte díl (5A) na místo, které je znázorněno
na obrázku. Je potřeba si na polohovat kabely od motoru tak,
aby nepřekážely sestavení.

10

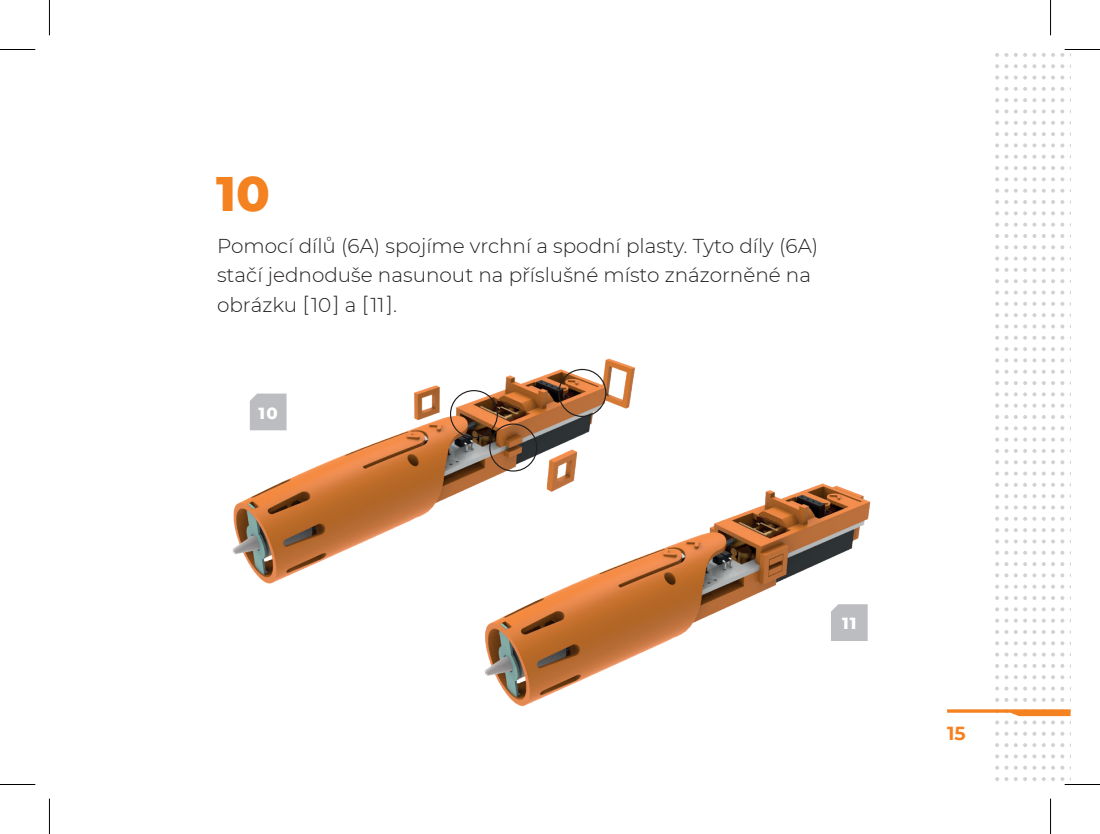
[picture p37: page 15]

Pomocí dílů (6A) spojíme vrchní a spodní plasty. Tyto díly (6A)
stačí jednoduše nasunout na příslušné místo znázorněné na
obrázku [10] a [11].

11

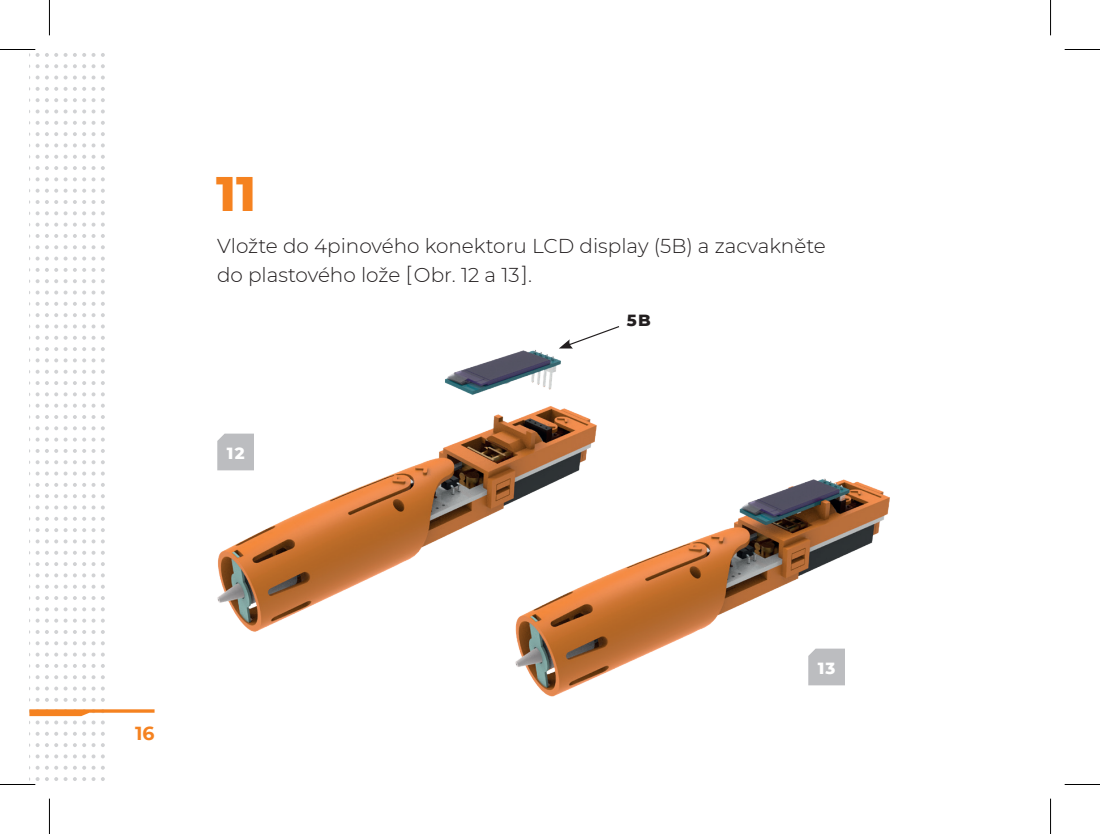
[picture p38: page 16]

Vložte do 4pinového konektoru LCD display (5B) a zacvakněte
do plastového lože [Obr. 12 a 13].

12

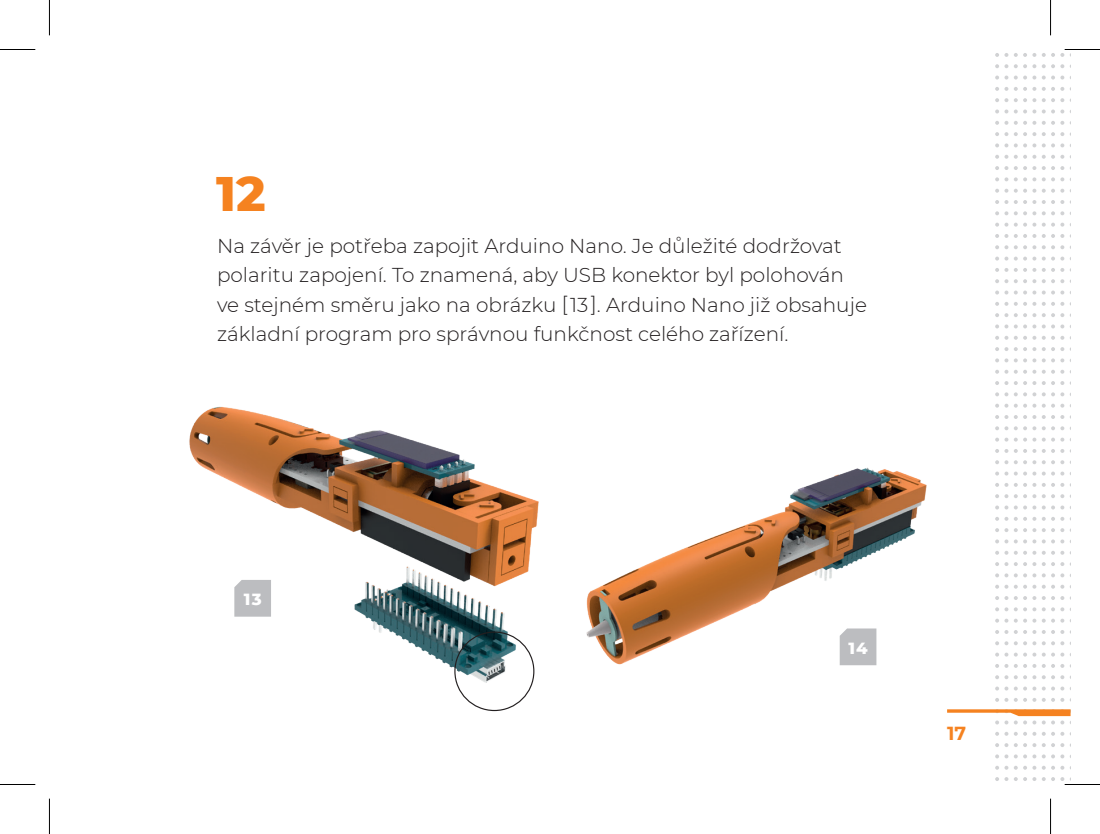
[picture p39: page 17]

Na závěr je potřeba zapojit Arduino Nano. Je důležité dodržovat
polaritu zapojení. To znamená, aby USB konektor byl polohován
ve stejném směru jako na obrázku [13]. Arduino Nano již obsahuje
základní program pro správnou funkčnost celého zařízení.

Zapojte přiložený USB kabel do zdroje napájení, kterým může být USB port v počítači, power banka s výstupem na 5 V nebo jakákoliv mobilní nabíječka (doporučujeme, aby mobilní nabíječka měla alespoň 1,5 A). Poté zapojíte druhý konec kabelu do 3Dsimo KIT. Po několika sekundách vám naběhne displej, kde se ukazuje postupné ohřívání na příslušnou teplotu a zvolený materiálový profil. Materiálové profily se dají přepínat dvěma tlačítky znázorněnými na [Obr. 15].

01

# PRVNÍ ZAPOJENÍ A OŽIVENÍ ZAŘÍZENÍ

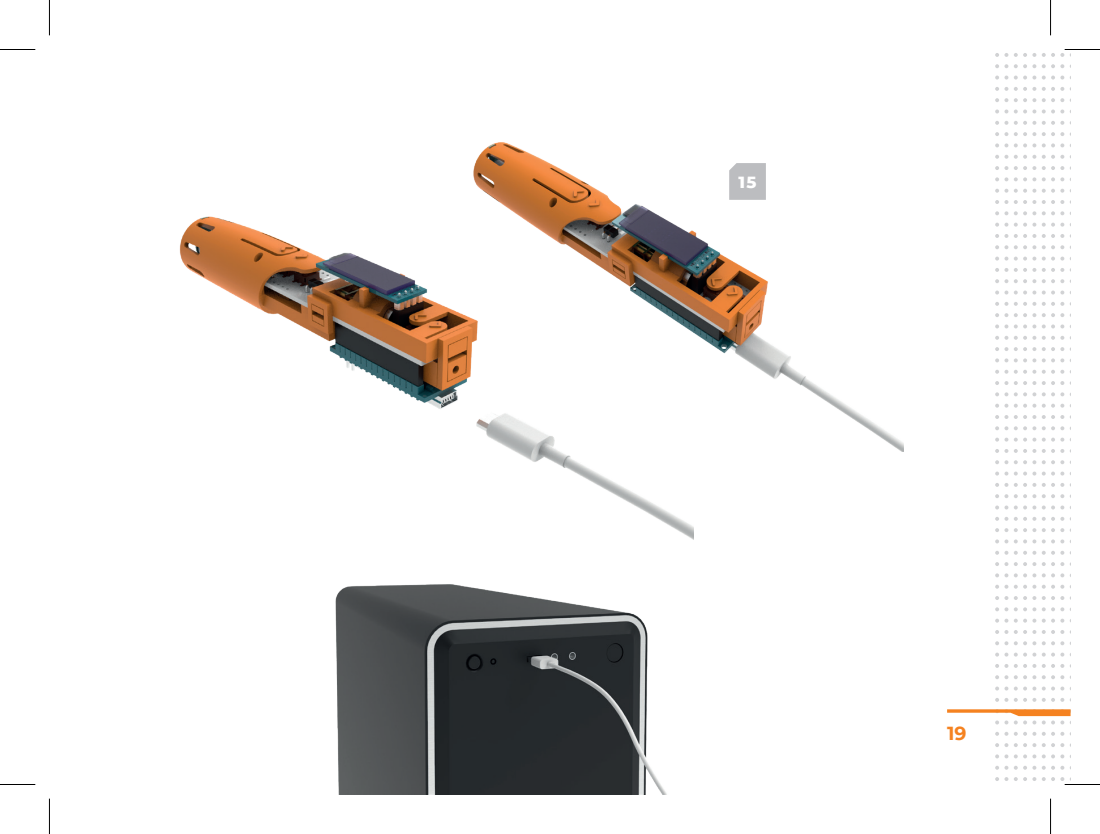
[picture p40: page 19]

Po zahřátí na požadovanou teplotu se vám aktivuje motor, který složí k posouvání filamentu. Ovládání motoru je dvěma předními tlačítky na [Obr. 16]. Tlačítko blíže k trysce posouvá materiál dopředu a druhé tlačítko po jednom kliknutí vysune celý materiál ven. Pokud vám tlačítka fungují opačně máte špatně zapojený motor a je potřeba otočit konektor motoru.

02

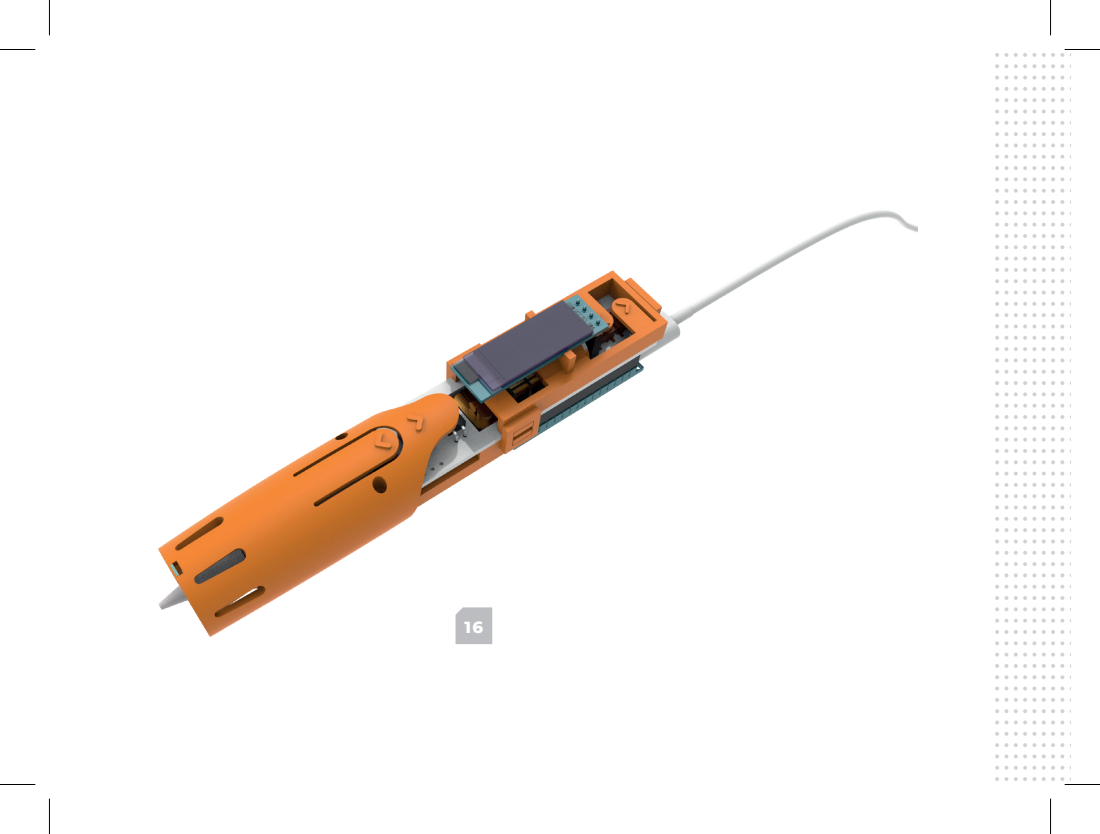
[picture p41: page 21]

Zavedení
Zavádějte vždy narovnaný materiál bez deformace. Filament vsunete do zadního otvoru a stisknete tlačítko dopředu [Obr. 16] zároveň musíte jemně na strunu zatlačit, aby se dostala do podávacího mechanizmu. Poté potrvá přibližně 10 s, než se struna dostane až k trysce a začne z 3Dsima KIT vytékat materiál.

01

# ZAVEDENÍ FILAMENTU A JEHO VÝMĚNA

02

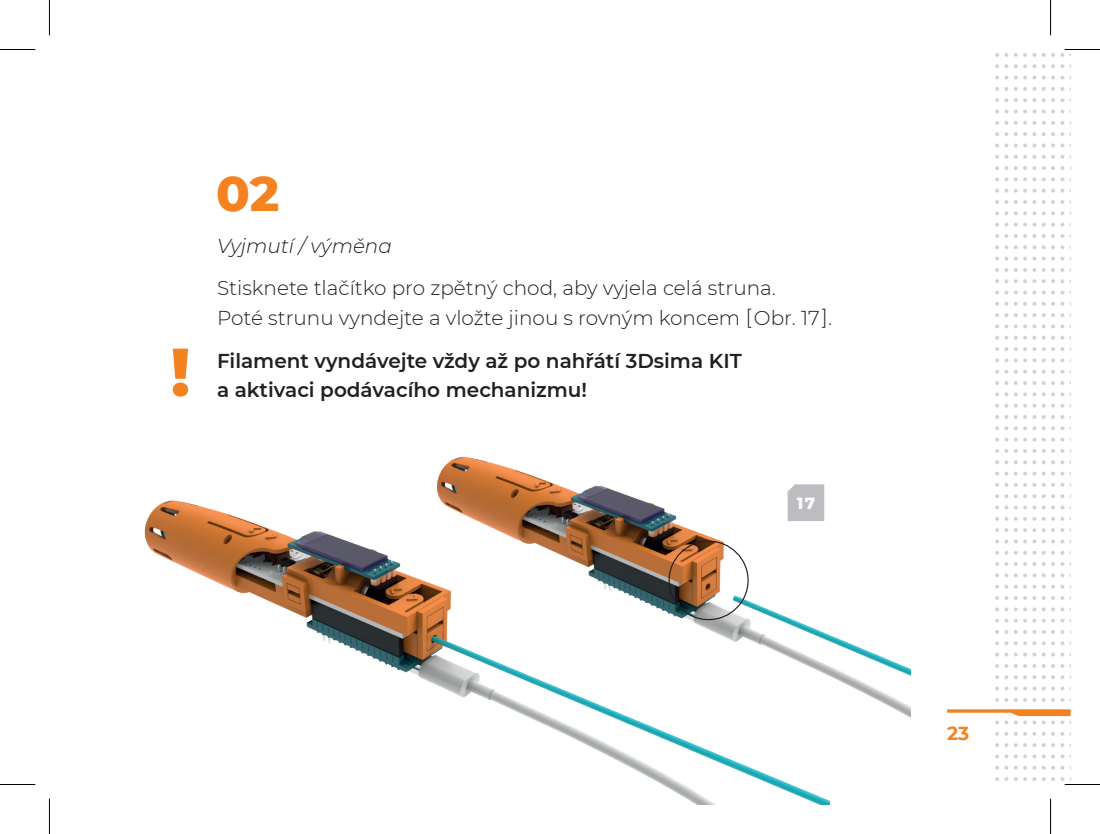
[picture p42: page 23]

Vyjmutí / výměna
Stisknete tlačítko pro zpětný chod, aby vyjela celá struna.
Poté strunu vyndejte a vložte jinou s rovným koncem [Obr. 17].
Filament vyndávejte vždy až po nahřátí 3Dsima KIT
a aktivaci podávacího mechanizmu!

### VAROVÁNÍ

### 1. Nebezpečí popálení. Tryska po zahřátí dosahuje vysokých

teplot až 250 °C. Nedotýkejte se trysky ani částí v její blízkosti, nebo roztaveného plastu, hrozí riziko popálení.

### 2. Zamezte styku těkavých a hořlavých látek s rozžhavenou

tryskou/hrotem.

3. Děti mohou 3Dsimo používat jen pod dohledem rodičů. Tento výrobek není hračka.

### 4. Nikdy nekreslete bez nasazeného předního dílu s laminátem

pod označením (4A). Mohlo by dojít k zničení trysky.

### 5. Při skladování, přepravě a provozu udržujte 3Dsimo v suchu

a vyvarujte se kontaktu s kapalinami.

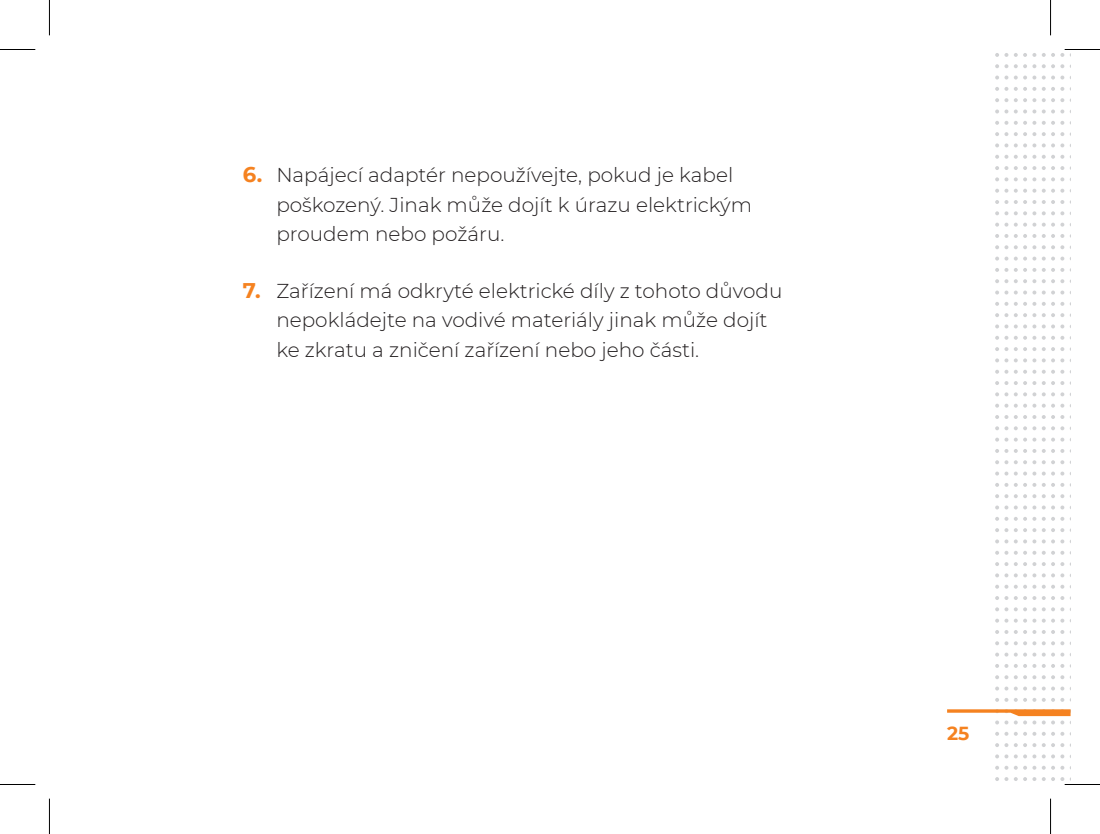
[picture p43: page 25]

6. Napájecí adaptér nepoužívejte, pokud je kabel
poškozený. Jinak může dojít k úrazu elektrickým
proudem nebo požáru.

7. Zařízení má odkryté elektrické díly z tohoto důvodu
nepokládejte na vodivé materiály jinak může dojít
ke zkratu a zničení zařízení nebo jeho části.

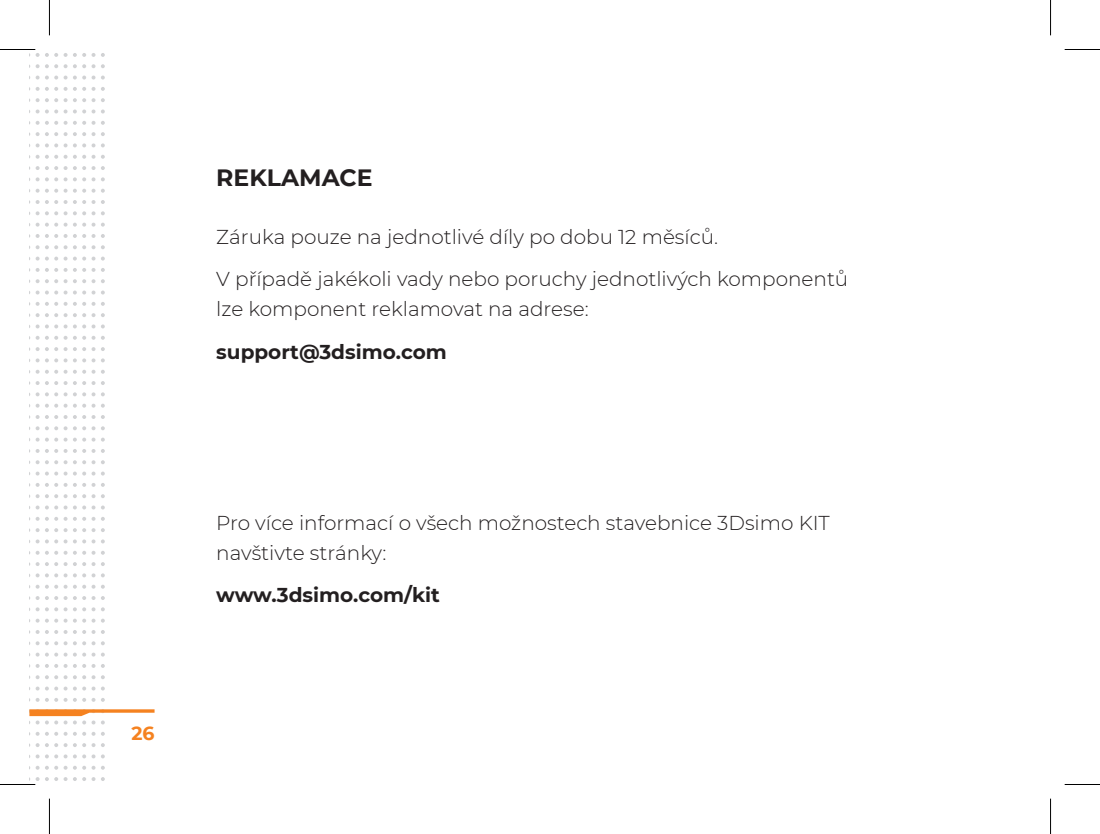
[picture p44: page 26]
REKLAMACE

Záruka pouze na jednotlivé díly po dobu 12 měsíců.
V případě jakékoli vady nebo poruchy jednotlivých komponentů
lze komponent reklamovat na adrese:
support@3dsimo.com

Pro více informací o všech možnostech stavebnice 3Dsimo KIT
navštivte stránky:
www.3dsimo.com/kit

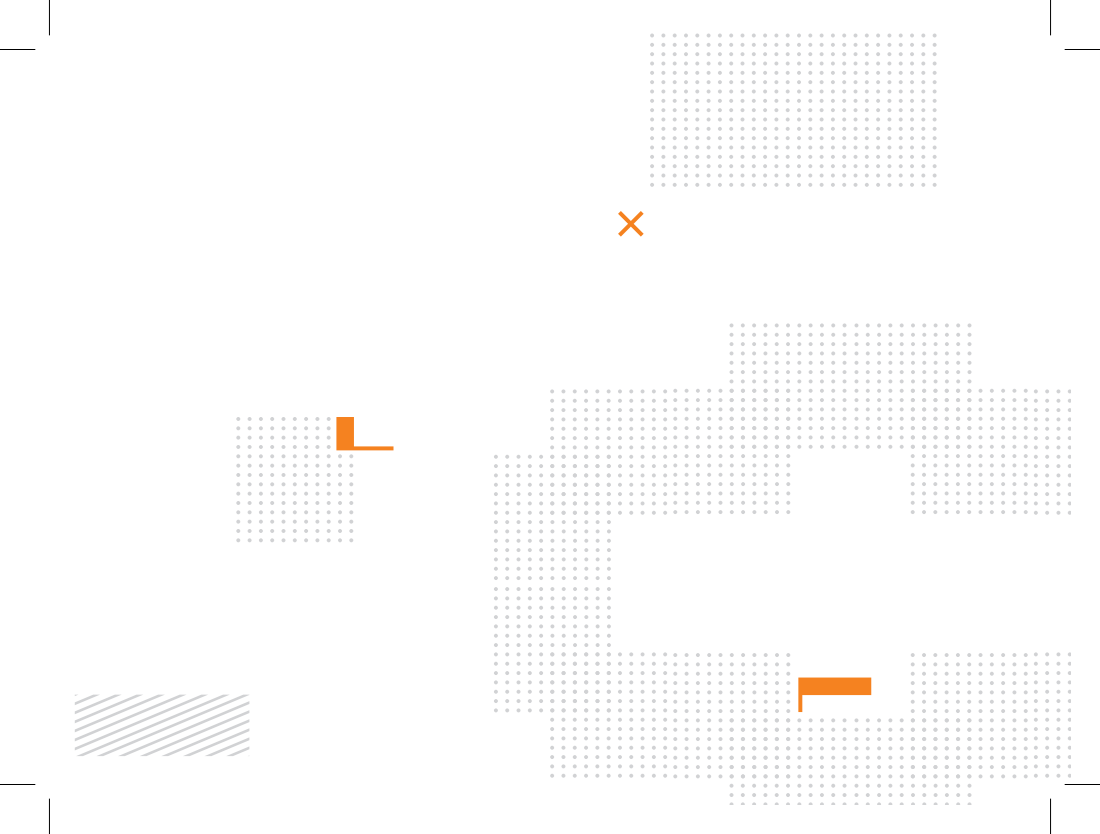
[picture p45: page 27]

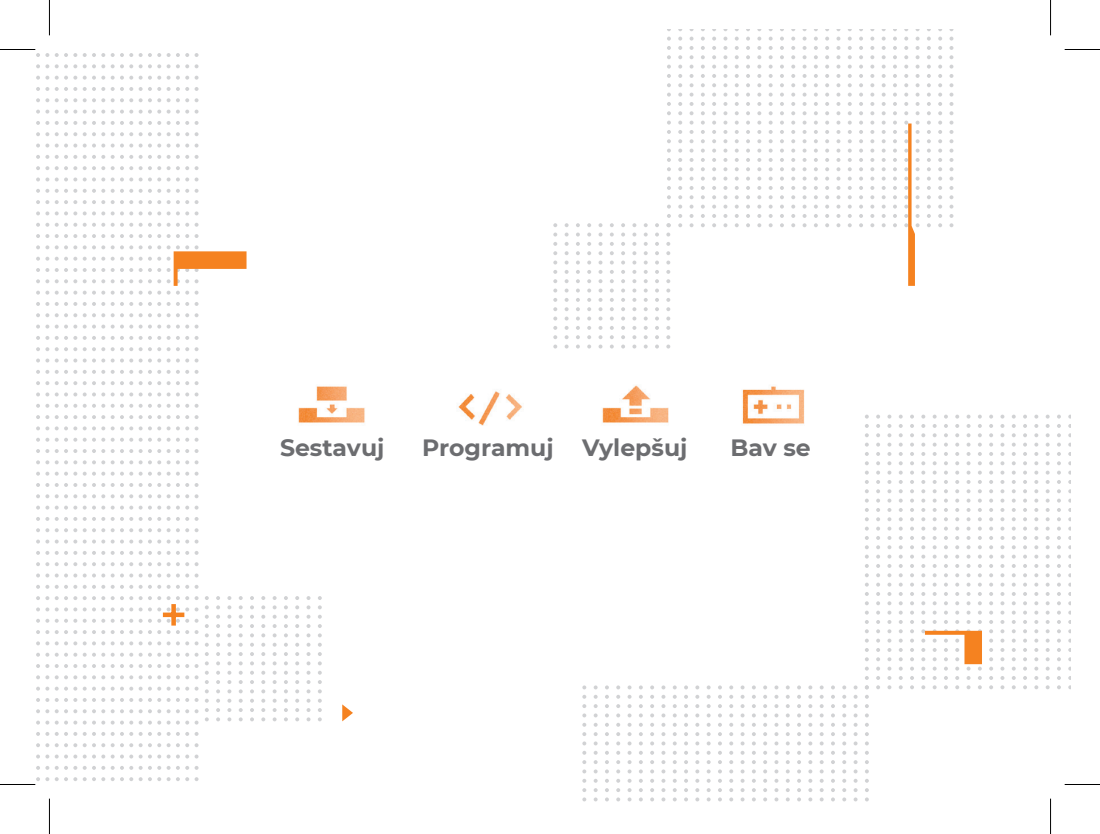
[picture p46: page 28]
Sestavuj Programuj Vylepšuj; Bav se

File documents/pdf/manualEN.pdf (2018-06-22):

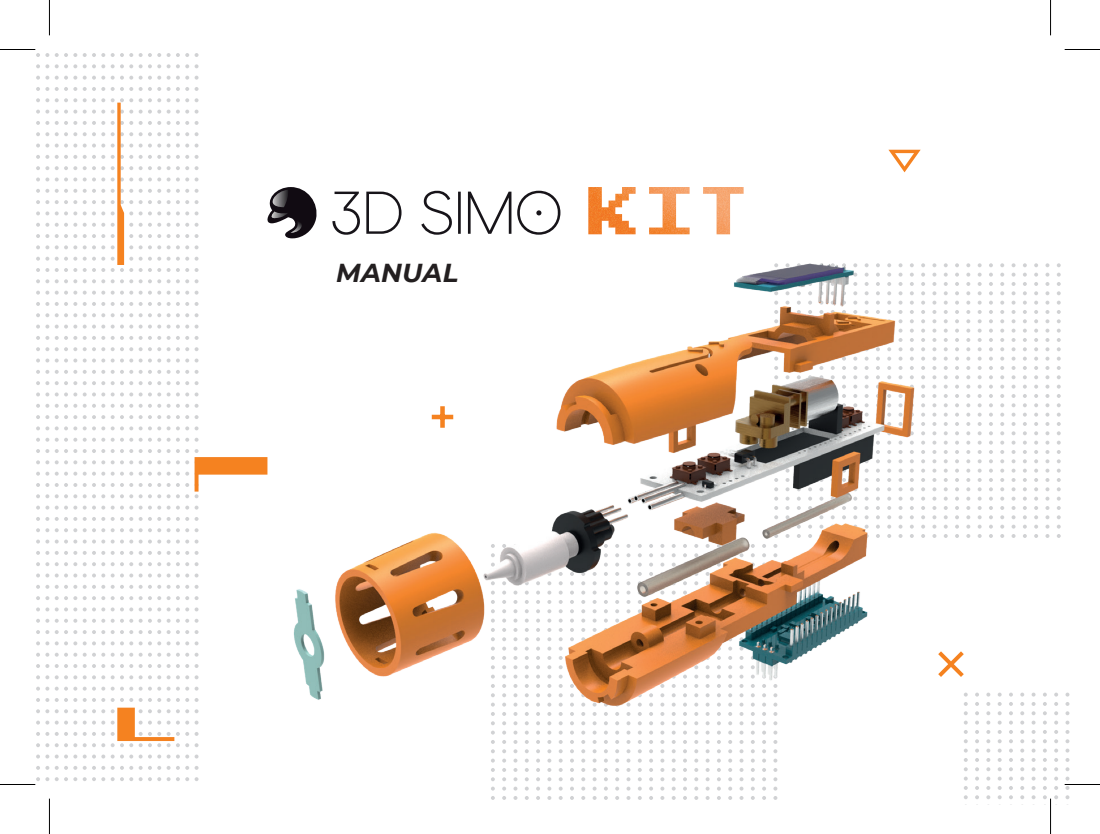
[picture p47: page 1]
MANUAL


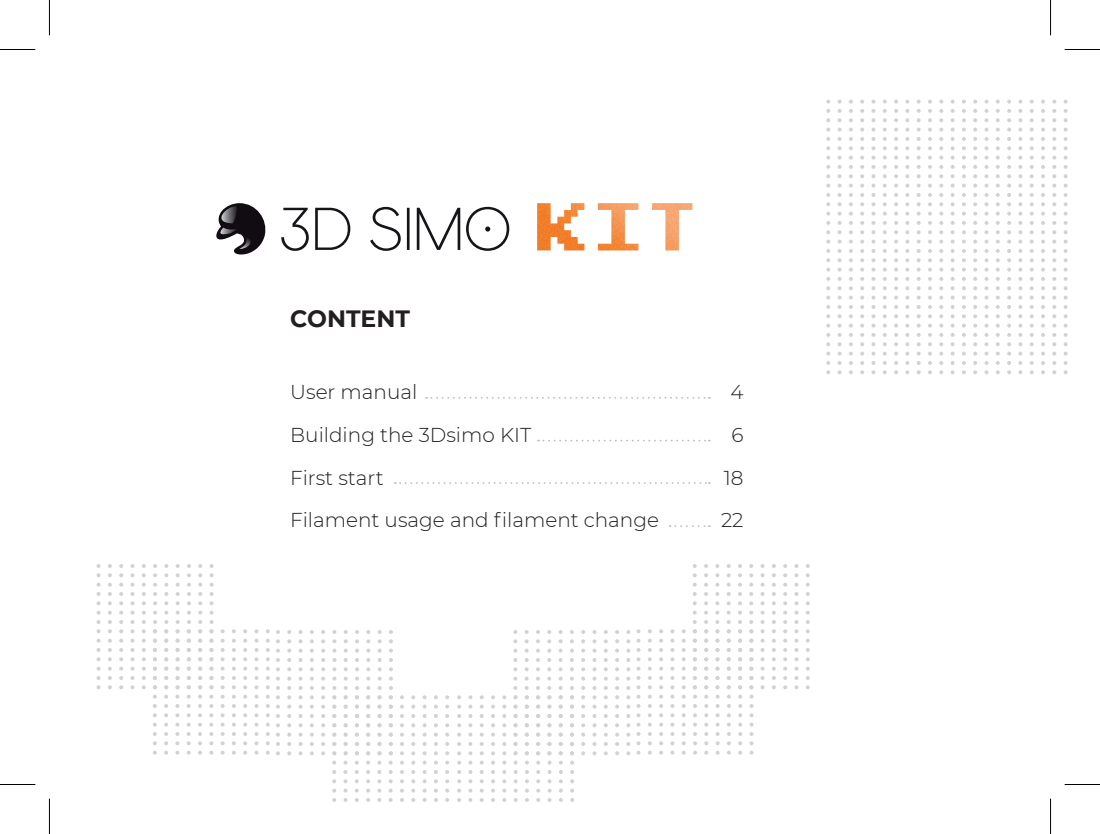
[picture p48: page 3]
CONTENT

User manual
Building the 3Dsimo KIT
First start
Filament usage and filament change

ٱ You have obtained multimaterial building kit, the 3Dsimo KIT. ٱ This kit is fully open source and uses fully programable Arduino Nano.
ٱ Time needed for the build: 15 – 30 min.
ٱ Before you begin with completing the 3Dsimo KIT, lay out all the parts on your work desk and make sure you have all the parts from the list.
ٱ At the bottom of the package you can find small parts (screws, nuts, Teflon tubes), as well as 5 m of ABS printing filament.
ٱ Filament compatible with 3Dsimo KIT is standard 3D printer filament, 1,75 mm in diameter.

# USER MANUAL

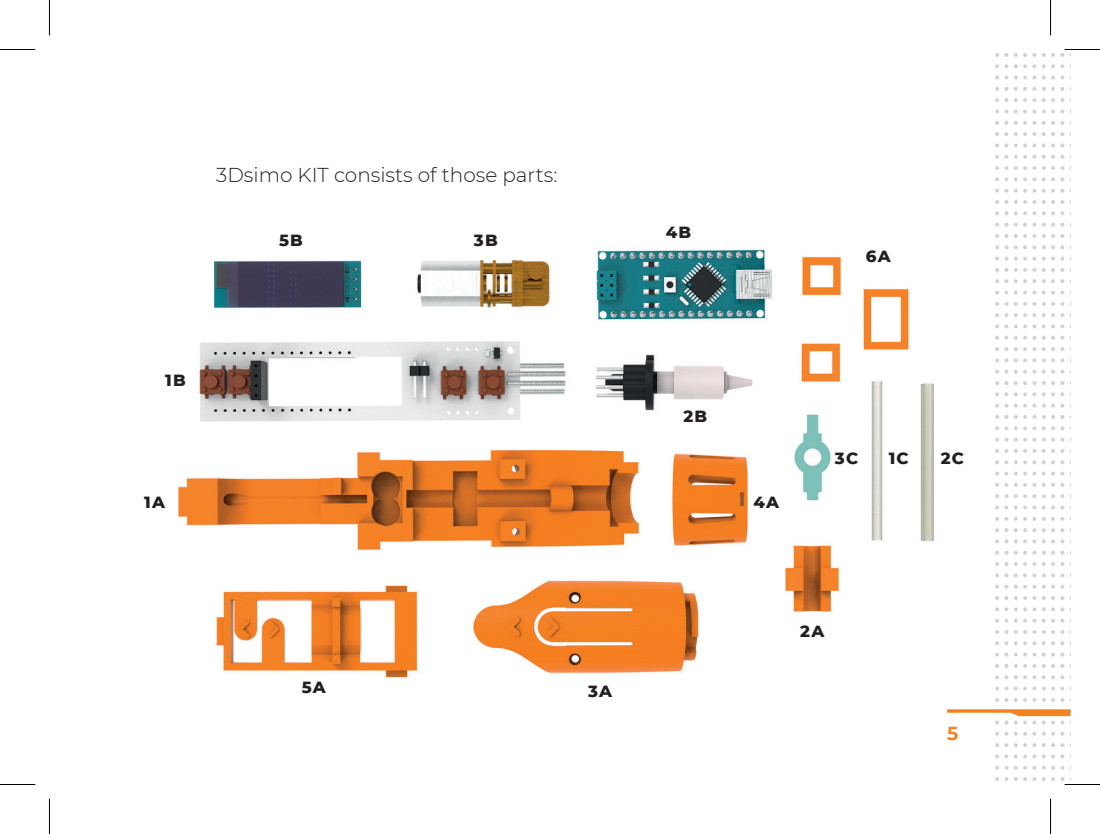
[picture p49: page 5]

3Dsimo KIT consists of those parts:

# BUILDING THE 3DSIMO KIT

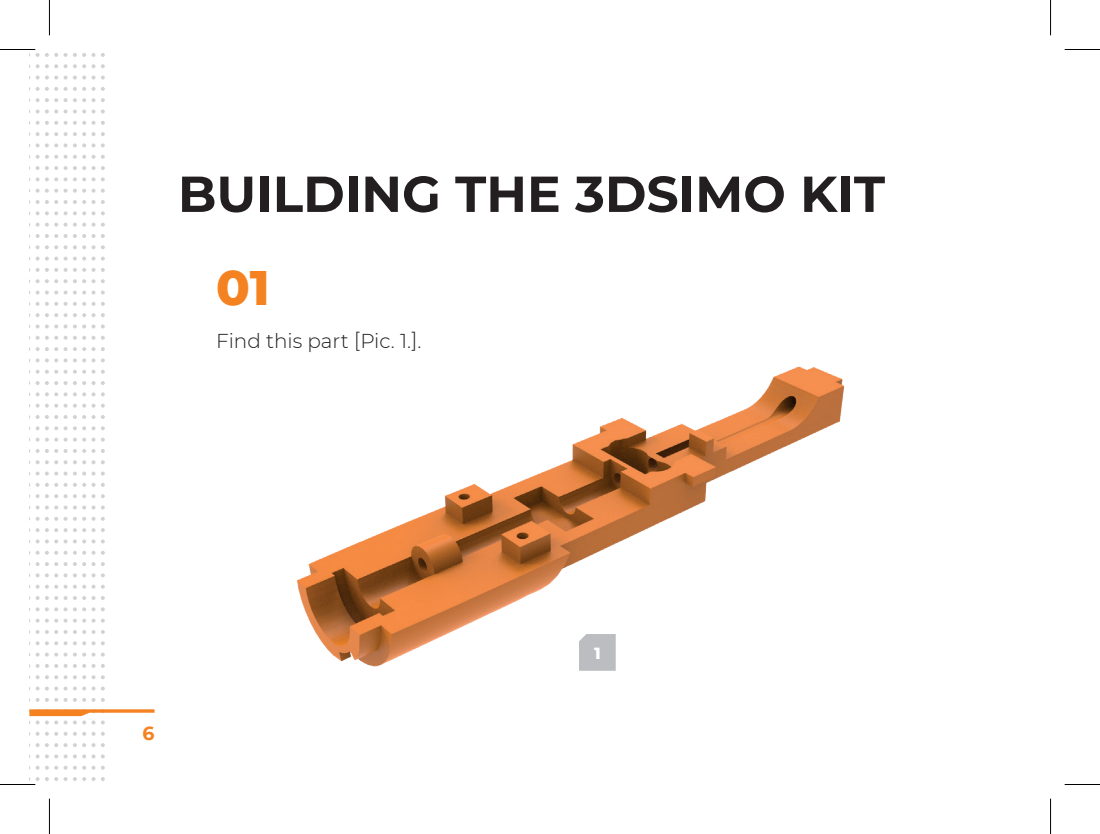
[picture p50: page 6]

Find this part [Pic. 1.].

02

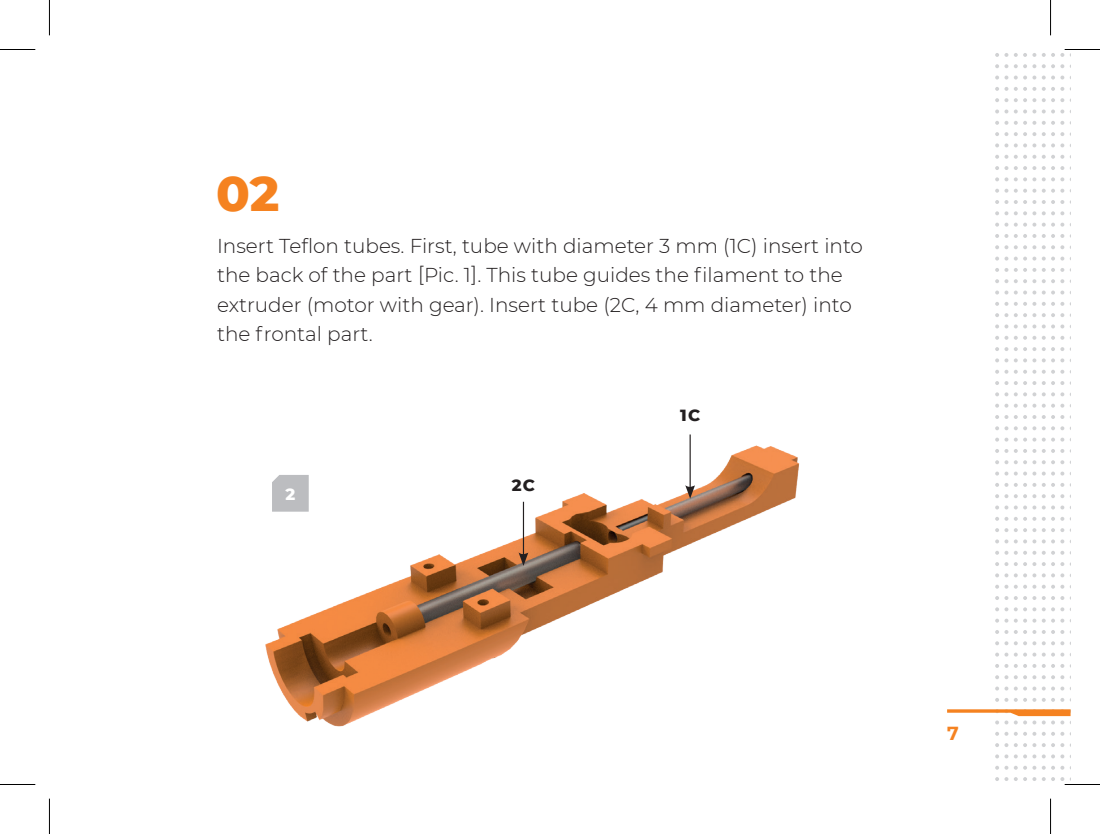
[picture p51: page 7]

Insert Teflon tubes. First, tube with diameter 3 mm (1C) insert into
the back of the part [Pic. 1]. This tube guides the filament to the
extruder (motor with gear). Insert tube (2C, 4 mm diameter) into
the frontal part.

03

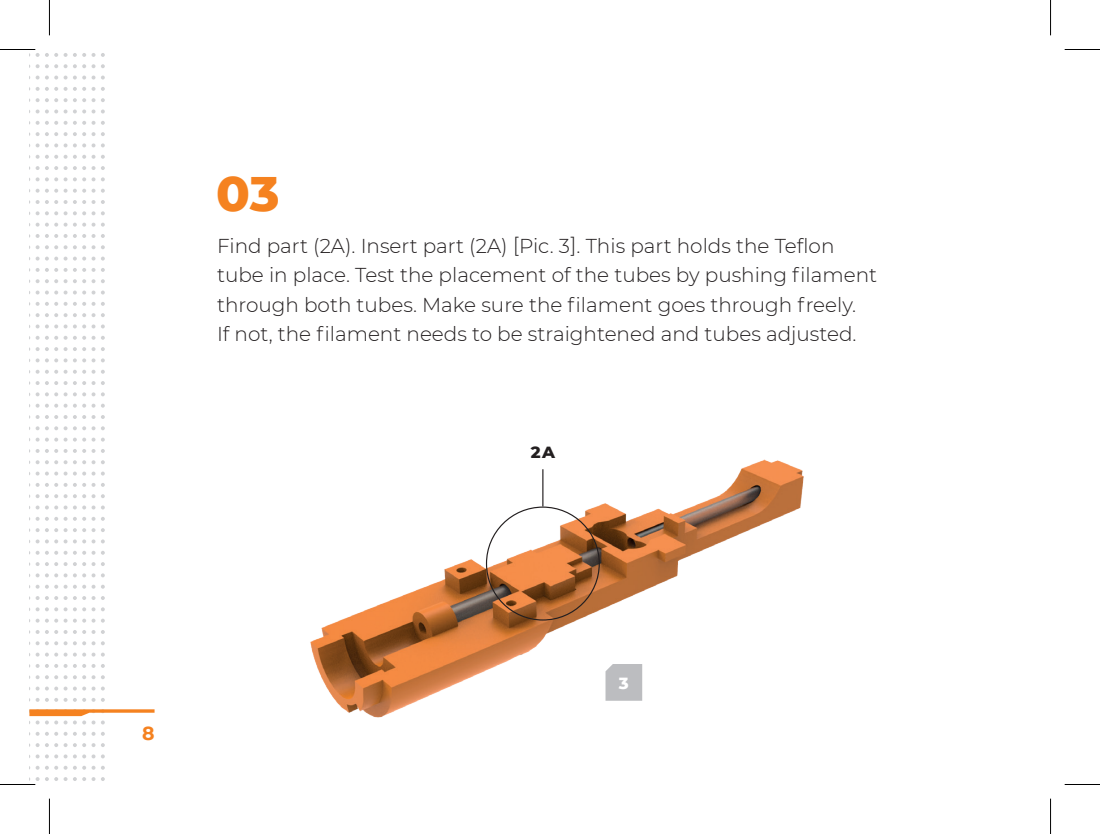
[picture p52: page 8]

Find part (2A). Insert part (2A) [Pic. 3]. This part holds the Teflon
tube in place. Test the placement of the tubes by pushing filament
through both tubes. Make sure the filament goes through freely.
If not, the filament needs to be straightened and tubes adjusted.

04

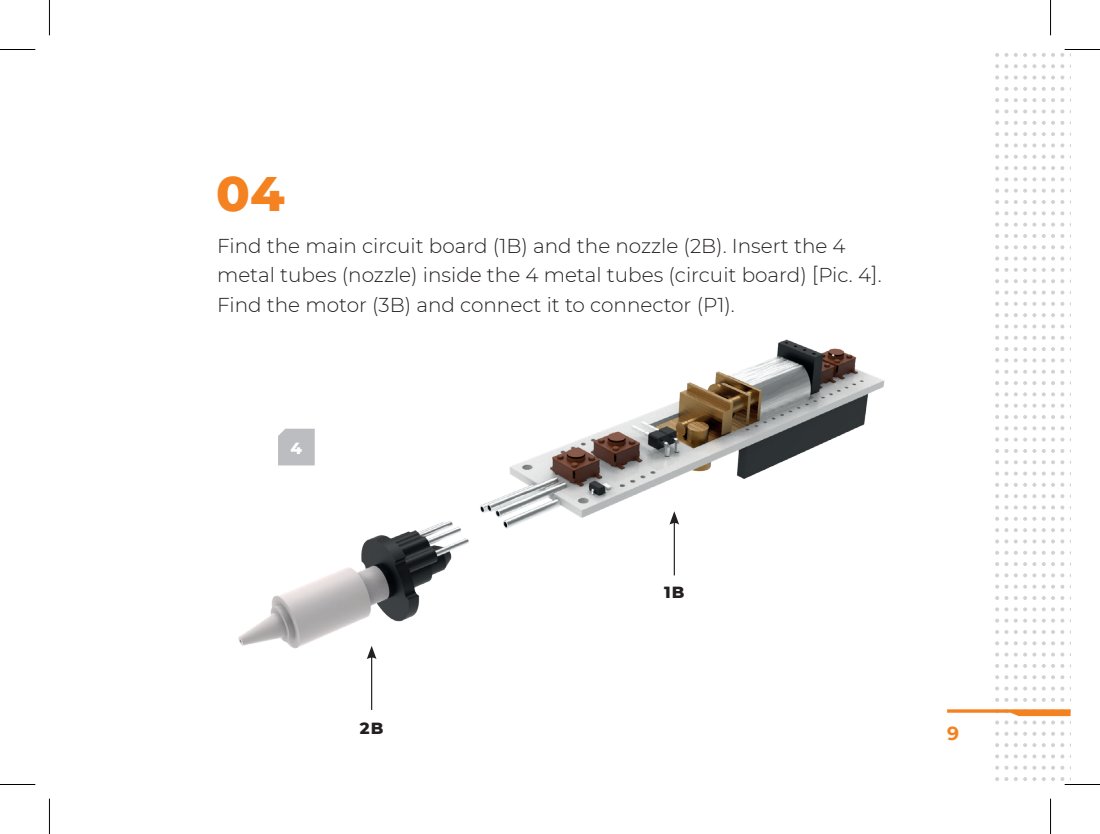
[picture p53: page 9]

Find the main circuit board (1B) and the nozzle (2B). Insert the 4
metal tubes (nozzle) inside the 4 metal tubes (circuit board) [Pic. 4].
Find the motor (3B) and connect it to connector (P1).

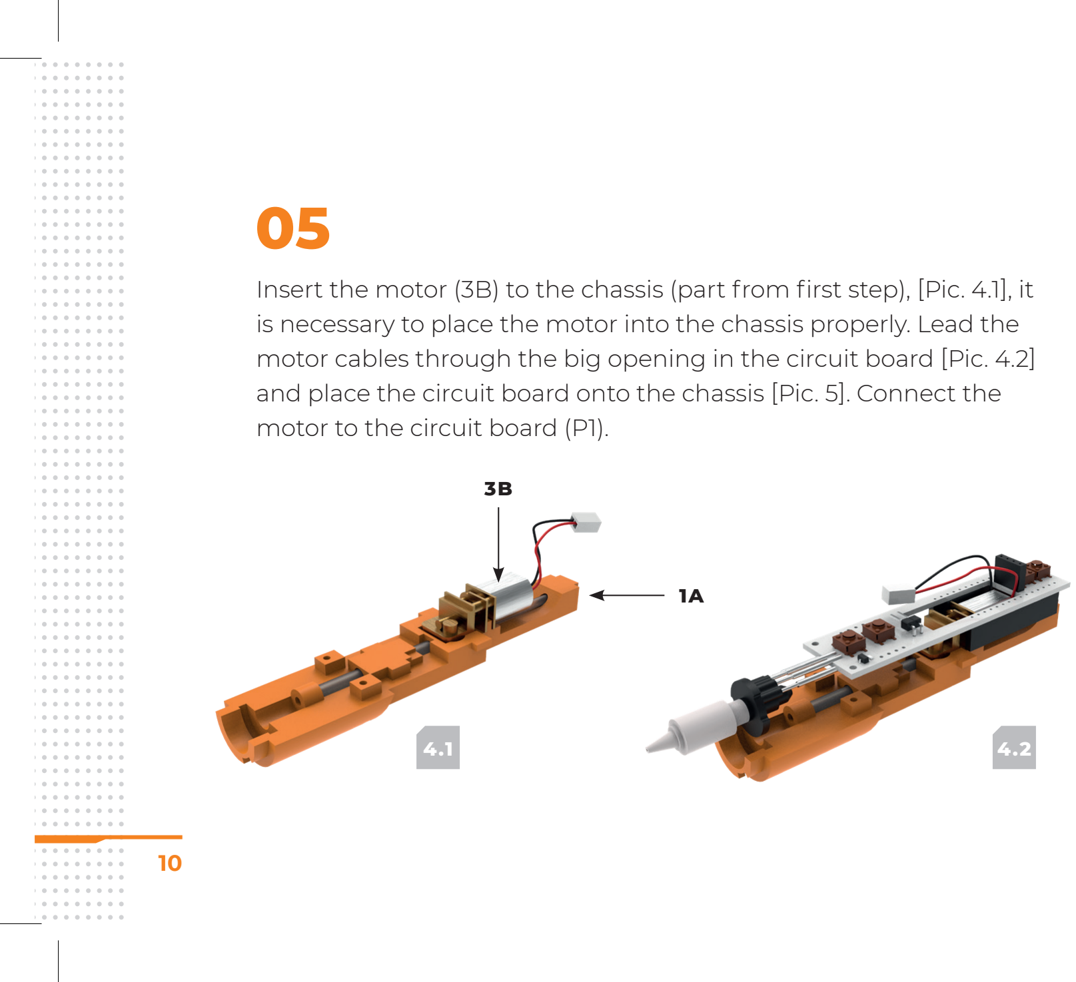
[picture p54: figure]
motor to the circuit board (P1).

Insert the motor (3B) to the chassis (part from first step), [Pic. 4.1], it is necessary to place the motor into the chassis properly. Lead the motor cables through the big opening in the circuit board [Pic. 4.2] and place the circuit board onto the chassis [Pic. 5]. Connect the

06

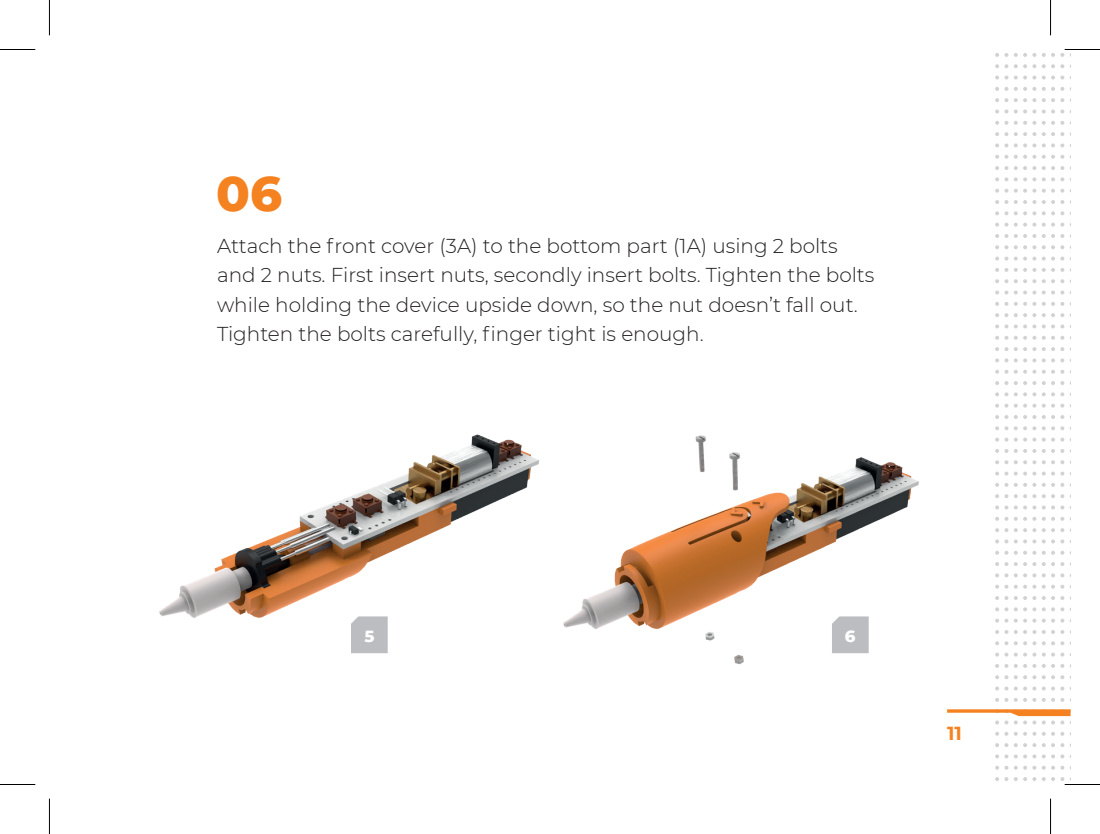
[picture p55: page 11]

Attach the front cover (3A) to the bottom part (1A) using 2 bolts
and 2 nuts. First insert nuts, secondly insert bolts. Tighten the bolts
while holding the device upside down, so the nut doesn’t fall out.
Tighten the bolts carefully, finger tight is enough.

07

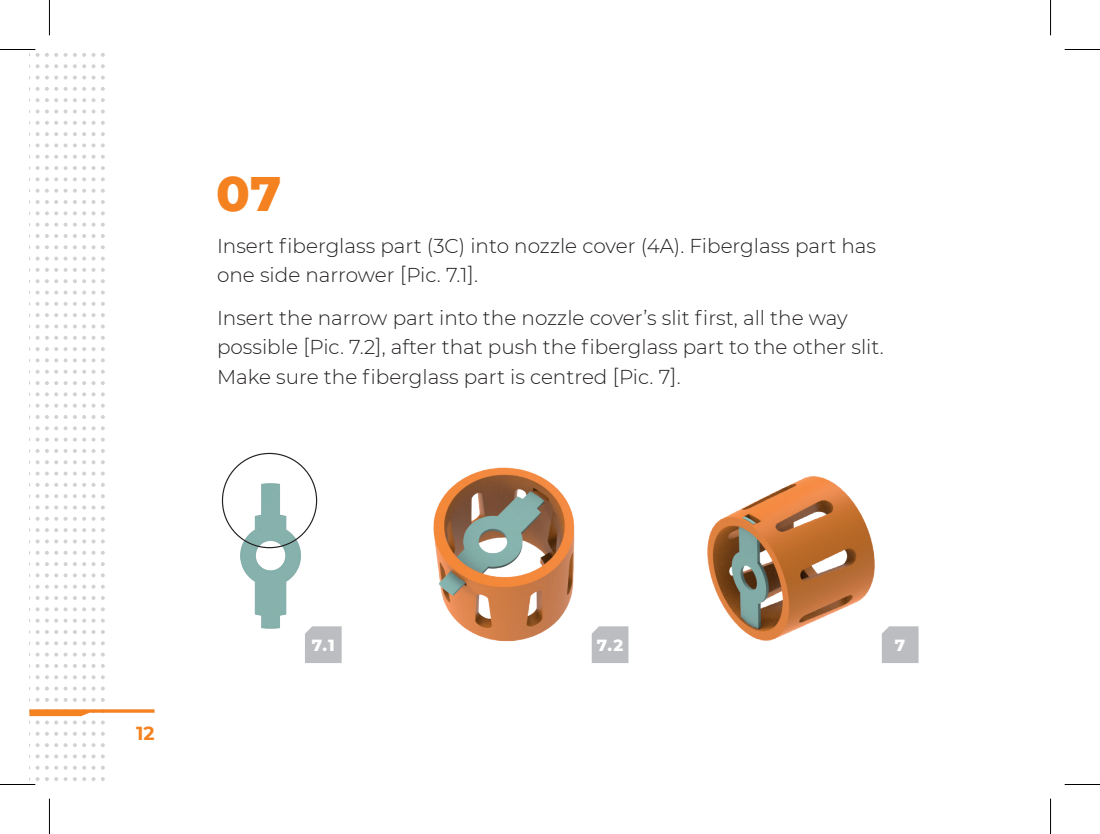
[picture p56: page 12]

Insert fiberglass part (3C) into nozzle cover (4A). Fiberglass part has
one side narrower [Pic. 7.1].
Insert the narrow part into the nozzle cover’s slit first, all the way
possible [Pic. 7.2], after that push the fiberglass part to the other slit.
Make sure the fiberglass part is centred [Pic. 7].

08

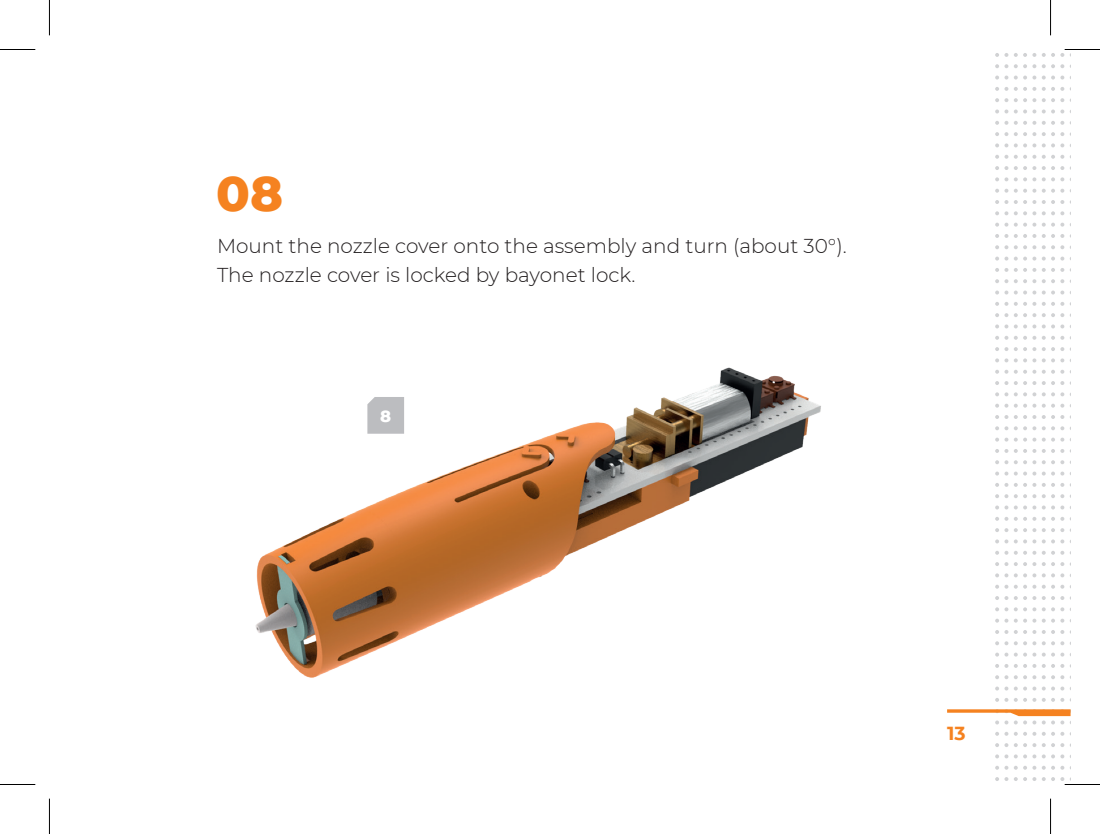
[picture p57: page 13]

Mount the nozzle cover onto the assembly and turn (about 30°).
The nozzle cover is locked by bayonet lock.

09

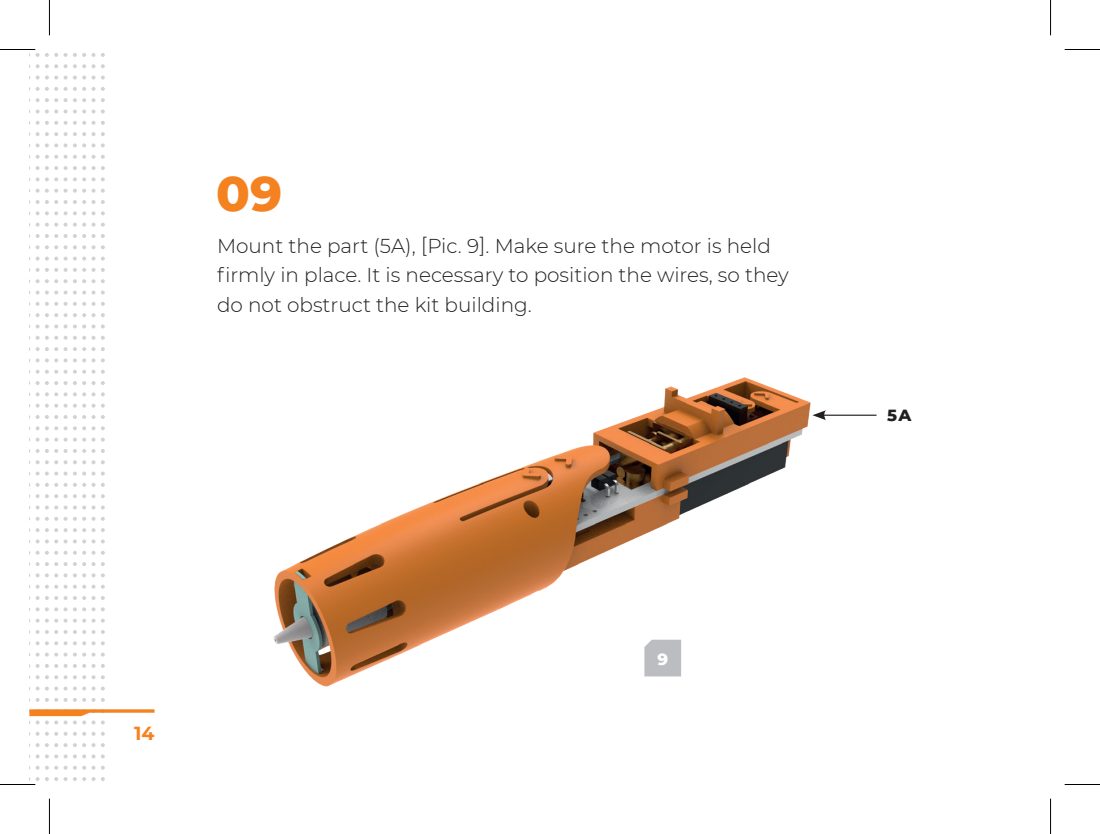
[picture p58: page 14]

Mount the part (5A), [Pic. 9]. Make sure the motor is held
firmly in place. It is necessary to position the wires, so they
do not obstruct the kit building.

10

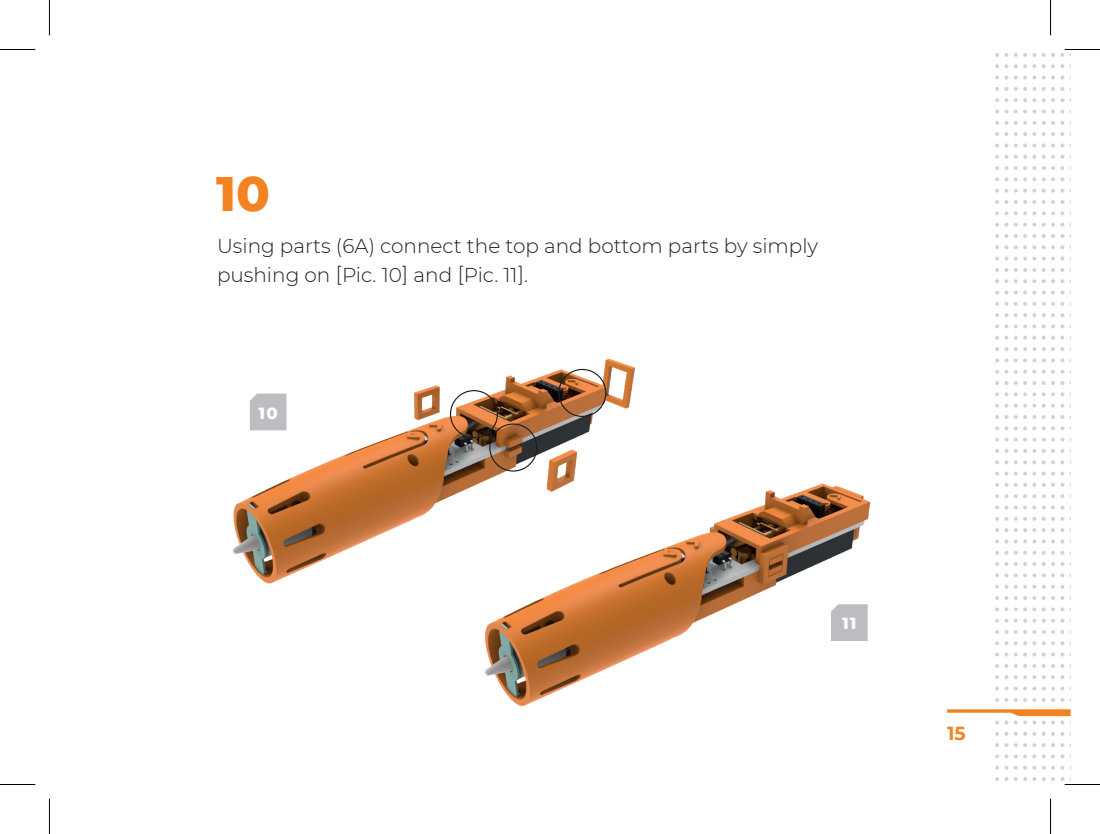
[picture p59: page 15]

Using parts (6A) connect the top and bottom parts by simply
pushing on [Pic. 10] and [Pic. 11].

11

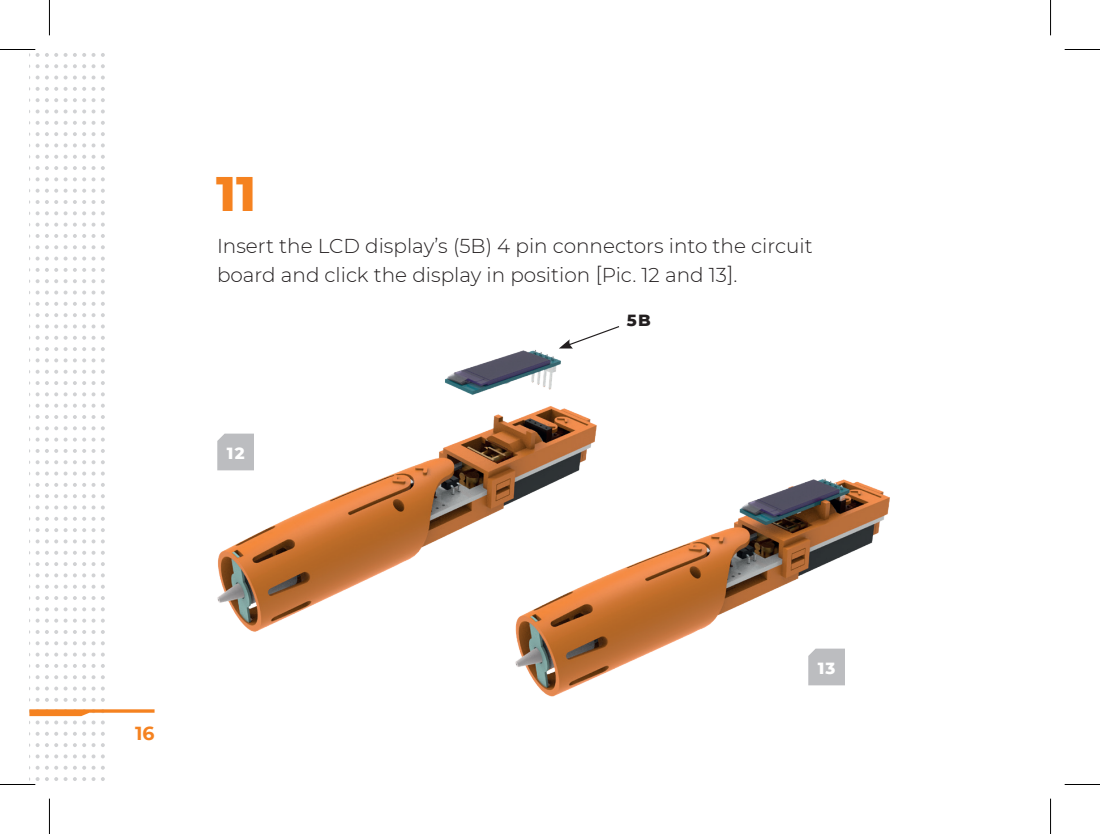
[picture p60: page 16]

Insert the LCD display’s (5B) 4 pin connectors into the circuit
board and click the display in position [Pic. 12 and 13].

12

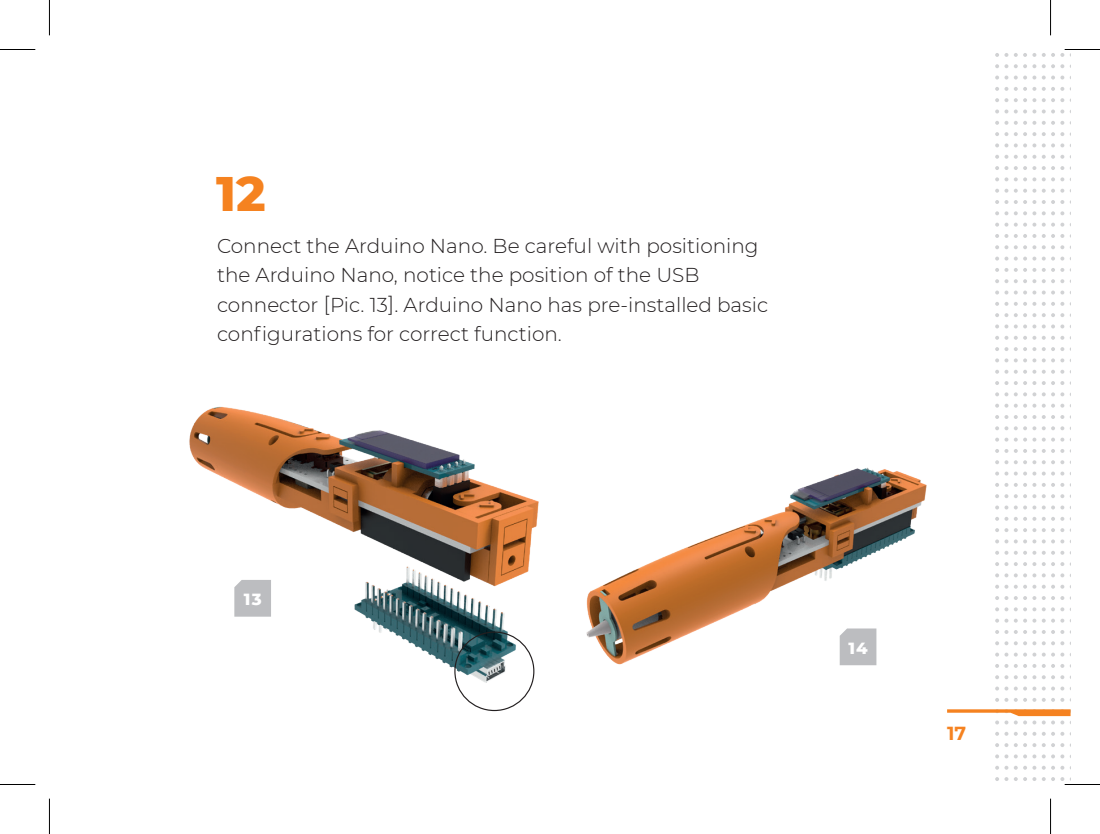
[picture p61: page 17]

Connect the Arduino Nano. Be careful with positioning
the Arduino Nano, notice the position of the USB
connector [Pic. 13]. Arduino Nano has pre-installed basic
configurations for correct function.

Connect the cable (included in the package) to electricity
(USB port on PC, power bank with 5V output or phone charger with 1.5A output minimum) and connect the cable to the 3Dsimo KIT. LCD display will turn on after few seconds, showing gradual heating of the nozzle, depending on chosen material heat profile. Material heat profiles can be changed using the buttons on the back of the 3Dsimo KIT [Pic. 15].

01

# FIRST START


When the nozzle is heated up to a temperature, filament feeding motor will be activated. The motor is operated via front two buttons [Pic. 16]. Button closer to the nozzle feeds the filament forward, the other button pulls out the filament after one click. If the buttons work the other way, the motor is plugged the wrong way and you have to unplug the motor, turn around the connector and plug again.

02


Using the filament:
Always use straightened filament without any deformations and with straight cut end. Push the filament into the opening on the back of 3Dsimo KIT, keep pushing as far as possible.
Push the front button and gently push the filament in, the feeding mechanism will do the rest. In about 10 seconds, the filament will start to come out of the 3Dsimo KIT.

01

# FILAMENT USAGE AND FILAMENT CHANGE

02

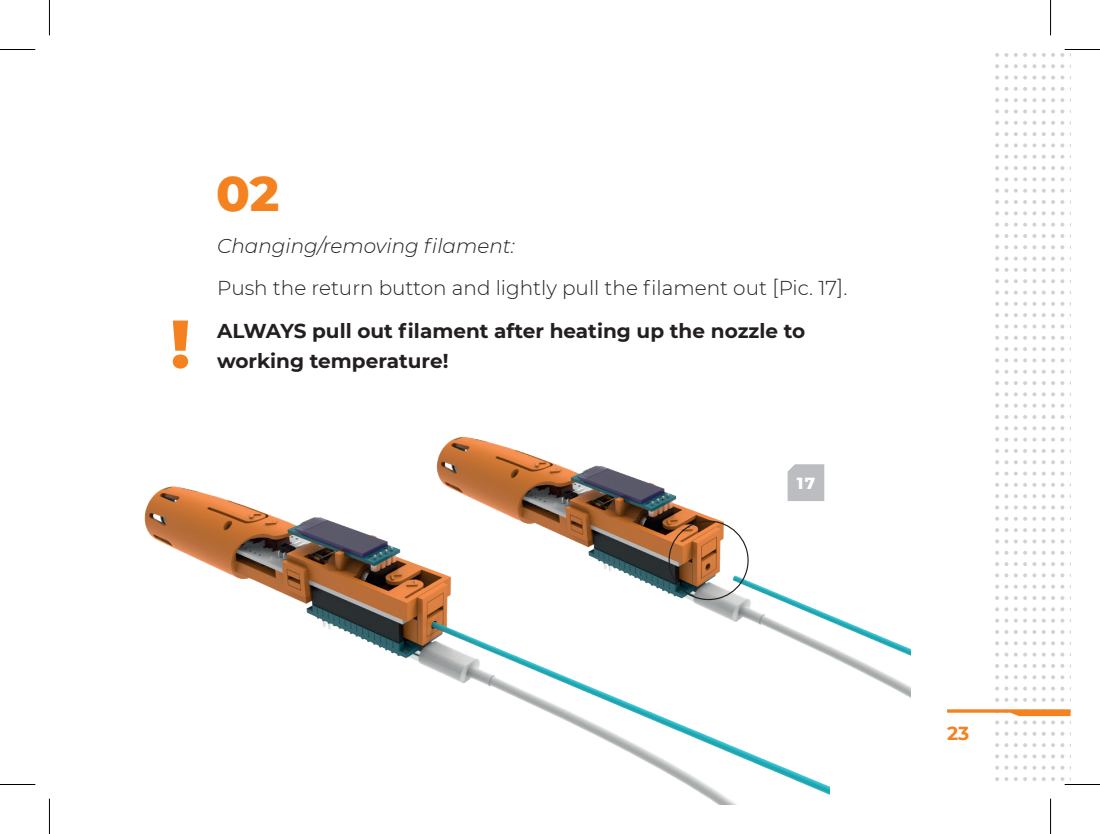
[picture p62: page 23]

Changing/removing filament:
Push the return button and lightly pull the filament out [Pic. 17].
ALWAYS pull out filament after heating up the nozzle to
working temperature!

### WARNING

### 1. Danger of burns. The nozzle heats up to 250 °C. Never touch

the nozzle or plastic parts near it.

2. Avoid contact of the nozzle and flammable substances.

### 3. This product is NOT a toy, children must be supervised when

using 3Dsimo KIT.

### 4. Never use this product without the fiberglass part, danger

of damage to the nozzle.

5. 3Dsimo KIT must be stored in dry environment, any contact with fluids can damage 3Dsimo KIT.

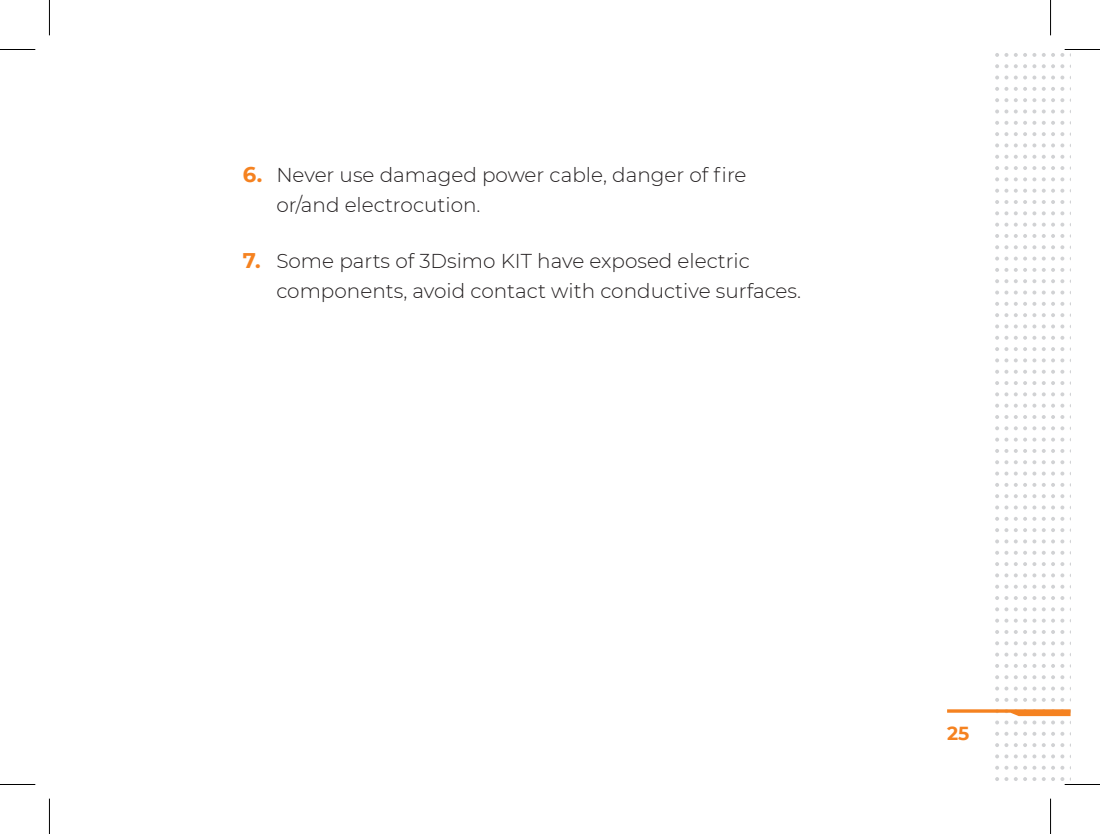
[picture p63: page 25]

6. Never use damaged power cable, danger of fire
or/and electrocution.

7. Some parts of 3Dsimo KIT have exposed electric
components, avoid contact with conductive surfaces.

WARRANTY

Warranty applies only to individual components for duration
of 12 months after purchase.
In case of warranty claim, contact our customer support:
support@3dsimo.com

For more information visit:
www.3dsimo.com/kit


Assemble; Program; Upgrade Have Fun

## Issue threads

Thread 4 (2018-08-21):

Display shows 153° as lowest "measured" temperatur

AnTi-ArT, 2018-08-21:
I like the new Off mode in 3DsimoKit_JC3D.ino (with target temperatur: 0°).
But I'm a bit confused: The "measured" temperature does never fall below 153°.
I took the leap and touched the 153°-hot-offmode-nozzle and (luckily) it was pretty cold. So I guess the value on the display is wrong? And the nozzle can heat to temperatures below 153°?

This would also be important for low temperature filaments like PCL. Which can be used at 50° - 70° and is therefore perfect for kids.

AnTi-ArT, 2018-08-28:
I'm working on a[ "freemode" control scheme for the 3Dsimo Kit](https://github.com/AnTi-ArT/3dsimo_kit/tree/Freemode/FW/3DsimoKit_Freemode) where the user can control temperature and Speed directly without profiles. However this limit of the temperature reading makes it impossible to use temperatures below 153°C.
Is this the minimum temperature of the tip?
It looks to me like the reading of the NTC is faulty. Shouldn't it be room temperature ~20°C when the tip is cold?

It would be cool if you can say what this reading of 153°C means. I'd prefer to not temper around with that code. Experimenting with the tip sounds dangerous...

najtvis, 2018-08-28:
When you are reading temperature 153C, this is correct. When you are trying to read temperature below 153C, you will always get 1020-1023 ADU from ADC converter as you can see in the following image. 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
Reading below 153C is only possible by changing resistor R4 to a higher value.

AnTi-ArT, 2018-08-28:
Thank you, this helped a lot. For now I implemented an "OFF" mode into my [Freemode project](https://github.com/AnTi-ArT/3dsimo_kit/tree/Freemode/FW/3DsimoKit_Freemode). It has to work with unmodified 3Dsimo Kit pens, too.

I will later research and figure out if I really want to change the resistor 😱

AnTi-ArT, 2018-09-04:
I noticed that the R4 resistor is extremely small and close to this black connector for the pins. I could never change it on my own! But if you ever put spare parts and alternative parts in your online shop, I would buy it!

kzvonicek, 2019-03-15:
Just bought the 3Dsimo kit and wondering if it is possible to configure it for PCL. Did you managed somehow to measure and set temp below 153°C and use PCL materials without changing the resistor? Or did someone tried to change the resistor?

How can I get the temperature calculation from ADU for different R4 resistances in case I decide to change the resisor? I assume I will ned to change the FW code as well.

Emmanouilpan, 2019-03-15:
I havent tried to set it below 155c. Try to change the temperature from the firmware code for pcl.

kzvonicek, 2019-03-15:
> I havent tried to set it below 155c. Try to change the temperature from the firmware code for pcl.

I assume from what AnTi-ArT and najtvis mentioned, that it cannot be done without HW tweaking ...

fosterswat, 2019-03-18:
Really nice thanks a lot for that but it is normal that after x press of a button it freeze ?

fosterswat, 2019-03-18:
I found that the problem was my usb to power adapter when iin my pc no problem but it always happen on my power adapter

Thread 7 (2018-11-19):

cannot compile, tried in arduino ide and in atom (platformio) get error- HELP

monterman, 2018-11-19:
here is the error:

> `C:\Arduino\libraries\ssd1306\src\ssd1306_generic.c: In function 'ssd1306_fillScreen':

C:\Arduino\libraries\ssd1306\src\ssd1306_generic.c:62:5: error: 'for' loop initial declarations are only allowed in C99 mode

     for(uint8_t m=(ssd1306_lcd.height >> 3); m>0; m--)

     ^

C:\Arduino\libraries\ssd1306\src\ssd1306_generic.c:62:5: note: use option -std=c99 or -std=gnu99 to compile your code

C:\Arduino\libraries\ssd1306\src\ssd1306_generic.c:64:9: error: 'for' loop initial declarations are only allowed in C99 mode

         for(uint8_t n=ssd1306_lcd.width; n>0; n--)

         ^

C:\Arduino\libraries\ssd1306\src\ssd1306_generic.c: In function 'ssd1306_clearScreen':

C:\Arduino\libraries\ssd1306\src\ssd1306_generic.c:76:5: error: 'for' loop initial declarations are only allowed in C99 mode

     for(uint8_t m=(ssd1306_lcd.height >> 3); m>0; m--)

     ^

C:\Arduino\libraries\ssd1306\src\ssd1306_generic.c:78:9: error: 'for' loop initial declarations are only allowed in C99 mode

         for(uint8_t n=ssd1306_lcd.width; n>0; n--)

         ^

C:\Arduino\libraries\ssd1306\src\ssd1306_generic.c: In function 'ssd1306_printFixedN':

C:\Arduino\libraries\ssd1306\src\ssd1306_generic.c:335:17: error: 'for' loop initial declarations are only allowed in C99 mode

                 for (uint8_t idx = 0; idx < 1<<(3-factor); idx++)

                 ^

C:\Arduino\libraries\ssd1306\src\ssd1306_generic.c:341:13: error: 'for' loop initial declarations are only allowed in C99 mode

             for (uint8_t z=(1<<factor); z>0; z--)

             ^

C:\Arduino\libraries\ssd1306\src\ssd1306_generic.c: In function 'ssd1306_drawHLine':

C:\Arduino\libraries\ssd1306\src\ssd1306_generic.c:633:5: error: 'for' loop initial declarations are only allowed in C99 mode

     for (uint8_t x = x1; x <= x2; x++)

     ^

C:\Arduino\libraries\ssd1306\src\ssd1306_generic.c: In function 'ssd1306_drawSprite':

C:\Arduino\libraries\ssd1306\src\ssd1306_generic.c:809:9: error: 'for' loop initial declarations are only allowed in C99 mode

         for (uint8_t i=0; i < sprite->w; i++)

         ^

C:\Arduino\libraries\ssd1306\src\ssd1306_generic.c:818:9: error: 'for' loop initial declarations are only allowed in C99 mode

         for (uint8_t i=0; i < sprite->w; i++)

         ^

C:\Arduino\libraries\ssd1306\src\ssd1306_generic.c: In function 'ssd1306_eraseSprite':

C:\Arduino\libraries\ssd1306\src\ssd1306_generic.c:834:5: error: 'for' loop initial declarations are only allowed in C99 mode

     for (uint8_t i=sprite->w; i > 0; i--)

     ^

C:\Arduino\libraries\ssd1306\src\ssd1306_generic.c:842:9: error: 'for' loop initial declarations are only allowed in C99 mode

         for (uint8_t i=sprite->w; i > 0; i--)

         ^

C:\Arduino\libraries\ssd1306\src\ssd1306_generic.c: In function 'ssd1306_eraseTrace':

C:\Arduino\libraries\ssd1306\src\ssd1306_generic.c:859:5: error: 'for' loop initial declarations are only allowed in C99 mode

     for(uint8_t y = y1; y <= y2; y++)

     ^

C:\Arduino\libraries\ssd1306\src\ssd1306_generic.c:862:9: error: 'for' loop initial declarations are only allowed in C99 mode

         for(uint8_t x = sprite->w; x > 0; x--)

         ^

C:\Arduino\libraries\ssd1306\src\ssd1306_generic.c:876:9: error: 'for' loop initial declarations are only allowed in C99 mode

         for(uint8_t y = sprite->ly >> 3; y <= (sprite->ly + 7) >> 3; y++)

         ^

C:\Arduino\libraries\ssd1306\src\ssd1306_generic.c:879:13: error: 'for' loop initial declarations are only allowed in C99 mode

             for(uint8_t x = x2 - x1 + 1; x > 0; x--)

             ^

Using library ssd1306 at version 1.7.0 in folder: C:\Arduino\libraries\ssd1306
Using library Wire at version 1.0 in folder: C:\Users\monte\AppData\Local\Arduino15\packages\arduino\hardware\avr\1.6.7\libraries\Wire
Using library EveryTimer at version 1.1.1 in folder: C:\Arduino\libraries\EveryTimer
exit status 1
Error compiling for board Arduino NANO`

monterman, 2018-11-28:
Hi Still nothing.   I tried with you Freemode version and cannot compile... new error I get in Platformio is:

`.pioenvs\nanoatmega168\src\3dsimo_EDIT.ino.cpp.o (symbol from plugin):(.text+0x0): first defined here
.pioenvs\nanoatmega168\src\main.cpp.o (symbol from plugin): In function `setup':
(.text+0x0): multiple definition of `loop'
.pioenvs\nanoatmega168\src\3dsimo_EDIT.ino.cpp.o (symbol from plugin):(.text+0x0): first defined here
C:\Users\monte\AppData\Local\Temp\ccz2LGpP.ltrans0.ltrans.o: In function `main':
<artificial>:(.text.startup+0x21e): undefined reference to `EveryTimer::Every(unsigned long, void (*)())'
<artificial>:(.text.startup+0x298): undefined reference to `EveryTimer::Update()'

C:\Users\monte\Local\Temp\ccz2LGpP.ltrans1.ltrans.o: In function `global constructors keyed to 65535_0_3dsimo_AFM_EDIT.ino.cpp.o.2711
':
<artificial>:(.text.startup+0x74): undefined reference to `EveryTimer::EveryTimer()'
collect2.exe: error: ld returned 1 exit status
*** [.pioenvs\nanoatmega168\firmware.elf] Error 1`

arcao, 2018-12-28:
No problem for me with latest Arduino IDE v1.8.8. I just installed SSD1806 OLED library and EasyTimer library as is specified in [this PDF document](https://github.com/3dsimo/3dsimo_kit/blob/master/documents/pdf/HW_FW_manualEN.pdf). I had only a little trouble with uploading to Ardunino Nano. The bundled Arduino Nano in the latest 3D Simo Kit version has actually ATmega328P MCU with old Arduino bootloader (57 600 kbps upload speed).

najtvis, 2020-02-04:
You are right @arcao, 3Dsimo KIT is using old bootloader and libraries from Arduino IDE. In this case use processor **Atmega328p (old bootloader)** which is in new versions of Arduino IDE.

For @monterman if you are using VS Code with Platformio or other IDE, it requires to add following libraries from Arduino IDE: SSD1306 and EasyTimer to your platform. The easiest way, how to get them is to install Arduino IDE, download the libraries and import them into your IDE. The libraries are located in your **Document** folder in **Arduino**.

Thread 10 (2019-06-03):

Arduino reboots after pressing x button

hoemph, 2019-06-03:
I found that the problem was my usb to power adapter when iin my pc no problem but it always happen on my power adapter

_Originally posted by @fosterswat in https://github.com/3dsimo/3dsimo_kit/issues/4#issuecomment-474142841_

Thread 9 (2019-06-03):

Arduino reboots after pressing x button

hoemph, 2019-06-03:

Closed 2019-06-03.

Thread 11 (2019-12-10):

Impossible to flash the 3DSimo Kit 2

ncarrier, 2019-12-10:
Hello,
Just received my shiny new 3DSimo Kit 2 today and wanted to modify the firmware, to add more plastic types (in particular, PCL).
I managed to clone the sources, fix the few compilation issues I had, but had no luck when trying to upload the generated firmware.
I'm using the Arduino IDE 1.8.10, I selected the Arduino Nano board, the ATmega328P processor (not the Old bootloader one). The serial port selected is the only one available and corresponds to the board.

When I try to upload the sketch, the compilation works well, but when trying to flash, I have the following:
```avrdude: Version 6.3-20190619
         Copyright (c) 2000-2005 Brian Dean, http://www.bdmicro.com/
         Copyright (c) 2007-2014 Joerg Wunsch

         System wide configuration file is "/home/nicolas/Logiciels/arduino-1.8.10-linux64/arduino-1.8.10/hardware/tools/avr/etc/avrdude.conf"
         User configuration file is "/home/nicolas/.avrduderc"
         User configuration file does not exist or is not a regular file, skipping

         Using Port                    : /dev/ttyUSB0
         Using Programmer              : arduino
         Overriding Baud Rate          : 115200
avrdude: stk500_getsync() attempt 1 of 10: not in sync: resp=0x00
avrdude: stk500_getsync() attempt 2 of 10: not in sync: resp=0x00
avrdude: stk500_getsync() attempt 3 of 10: not in sync: resp=0x00
avrdude: stk500_getsync() attempt 4 of 10: not in sync: resp=0x00
avrdude: stk500_getsync() attempt 5 of 10: not in sync: resp=0x00
avrdude: stk500_getsync() attempt 6 of 10: not in sync: resp=0x00
avrdude: stk500_getsync() attempt 7 of 10: not in sync: resp=0x00
avrdude: stk500_getsync() attempt 8 of 10: not in sync: resp=0x00
avrdude: stk500_getsync() attempt 9 of 10: not in sync: resp=0x00
avrdude: stk500_getsync() attempt 10 of 10: not in sync: resp=0x00

avrdude done.  Thank you.

An error occurred while uploading the sketch
```

An idea of what I could be doing wrong?

I don't think that really matters, but I'm using debian linux buster (10).

Thank you by advance.

najtvis, 2019-12-11:
Hello,

You are right, Board is Arduino Nano and processors is ATMEGA328P.

It seems, you have different configurations when you are uploading the firmware. Arduino Nano is using 57600 Baud rate, but your Arduino tries it to upload at Baud rate 115200. Are you able to reduce the Baud rate?

When we are verifying the bootloader and connection between PC and 3Dsimo KIT2, using the following command:

```
avrdude -V -c arduino -b 57600 -patmega328p -Pcom1 -D -Uflash:w:3DsimoKit_v2.ino.without_bootloader.hex:i
```

ncarrier, 2019-12-11:
Hello,
Thank you for trying to help me, unfortunately, my 3DSimo Kit 2 already broke in less than 1 day :/
The USB plug got de-soldered.

So I'll come back to you as soon as I have a solution from the 3DSimo after sales, which I just contacted.

stevegood, 2019-12-14:
I am having the same issue but with the original Kit.  I've tried using both `ATMega328P` and `ATMega168`.  Everything compiles fine but uploading the sketch yields the following:

```//bin/avrdude -C//etc/avrdude.conf -v -patmega168 -carduino -P/dev/ttyUSB0 -b19200 -D -Uflash:w:/tmp/arduino_build_18532/3DsimoKit.ino.hex:i

avrdude: Version 6.3, compiled on May  8 2019 at 19:46:05
         Copyright (c) 2000-2005 Brian Dean, http://www.bdmicro.com/
         Copyright (c) 2007-2014 Joerg Wunsch

         System wide configuration file is "//etc/avrdude.conf"
         User configuration file is "/home/steve/.avrduderc"
         User configuration file does not exist or is not a regular file, skipping

         Using Port                    : /dev/ttyUSB0
         Using Programmer              : arduino
         Overriding Baud Rate          : 19200
avrdude: stk500_recv(): programmer is not responding
avrdude: stk500_getsync() attempt 1 of 10: not in sync: resp=0x00
avrdude: stk500_recv(): programmer is not responding
avrdude: stk500_getsync() attempt 2 of 10: not in sync: resp=0x00
avrdude: stk500_recv(): programmer is not responding
avrdude: stk500_getsync() attempt 3 of 10: not in sync: resp=0x00
avrdude: stk500_recv(): programmer is not responding
avrdude: stk500_getsync() attempt 4 of 10: not in sync: resp=0x00
avrdude: stk500_recv(): programmer is not responding
avrdude: stk500_getsync() attempt 5 of 10: not in sync: resp=0x00
avrdude: stk500_recv(): programmer is not responding
avrdude: stk500_getsync() attempt 6 of 10: not in sync: resp=0x00
avrdude: stk500_recv(): programmer is not responding
avrdude: stk500_getsync() attempt 7 of 10: not in sync: resp=0x00
avrdude: stk500_recv(): programmer is not responding
avrdude: stk500_getsync() attempt 8 of 10: not in sync: resp=0x00
avrdude: stk500_recv(): programmer is not responding
avrdude: stk500_getsync() attempt 9 of 10: not in sync: resp=0x00
avrdude: stk500_recv(): programmer is not responding
avrdude: stk500_getsync() attempt 10 of 10: not in sync: resp=0x00

avrdude done.  Thank you.

Problem uploading to board.  See http://www.arduino.cc/en/Guide/Troubleshooting#upload for suggestions.
```

FWIW, I get the same issue when using Platform.IO.

blacklistedoperative, 2019-12-22:
Arduino: 1.8.10 (Windows 10), Board: "Arduino Nano, ATmega328P"

In function 'heating',

    inlined from 'timerAction' at C:\Users\Owner\Documents\Arduino\sketch_dec21a\sketch_dec21a.ino:270:37:

C:\Users\Owner\Documents\Arduino\sketch_dec21a\sketch_dec21a.ino:209:11: warning: 'memset' writing 256 bytes into a region of size 128 overflows the destination [-Wstringop-overflow=]

     memset(tempAvg, 0, sizeof(tempAvg)*sizeof(int));

           ^

Sketch uses 11116 bytes (36%) of program storage space. Maximum is 30720 bytes.
Global variables use 694 bytes (33%) of dynamic memory, leaving 1354 bytes for local variables. Maximum is 2048 bytes.
avrdude: stk500_getsync() attempt 1 of 10: not in sync: resp=0x00
avrdude: stk500_getsync() attempt 2 of 10: not in sync: resp=0x00
avrdude: stk500_getsync() attempt 3 of 10: not in sync: resp=0x00
avrdude: stk500_getsync() attempt 4 of 10: not in sync: resp=0x00
avrdude: stk500_getsync() attempt 5 of 10: not in sync: resp=0x00
avrdude: stk500_getsync() attempt 6 of 10: not in sync: resp=0x00
avrdude: stk500_getsync() attempt 7 of 10: not in sync: resp=0x00
avrdude: stk500_getsync() attempt 8 of 10: not in sync: resp=0x00
avrdude: stk500_getsync() attempt 9 of 10: not in sync: resp=0x00
avrdude: stk500_getsync() attempt 10 of 10: not in sync: resp=0x00
An error occurred while uploading the sketch

blacklistedoperative, 2019-12-22:
same worst purchase I've ever made

zsmadmin, 2020-01-13:
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

Hallo,
happened with my two new 3d simo kit pens just recieved in january...
have a friend who soldered them back to the motherboard
in my eyes the issue is in the model design, as there is too much space around the USB connector.
currently working on a Kids friendly model version with a secure USB connector
it should help a lot

stevegood, 2020-01-13:
FWIW, I contacted their support email and they are replacing the board on my kit 2.  It seems they had a bad batch of boards where the connector was coming off.

ncarrier, 2020-01-17:
Yay it worked!
I just received my replacement motherboard and I just started sculpting using PCL.
I have some issues on the mechanical side, but AFAIC, I have no real problem to modify and flash the software.

In order to flash, I copied the command-line the arduino IDE attempted to use and executed it manually with the correct baudrate of 57600 as instructed by @najtvis, so thank you very much!

One question though, I couldn't find a way to modify the baudrate the IDE will use to flash the board, is there a way to do it?
Otherwise I have to do it in two steps, it's not a big deal, yet it's not practical...

zsmadmin, 2020-01-21:
Dear  @ncarrier  and @stevegood,
honestly am fairly new (thats an overstatement) to the modding of Arduino motherboards (or any in general).
i would like to ask if there would be any chance you submit some end-to-end guide for dummies how to upgrade the KIT2 software with your enhancements?

or an upgrade something similar as @anti-art did in his feemode FW? (free regulation of temprature and speed)

blacklistedoperative, 2020-02-01:
It's more than just plugging it in to your pc you need a flashing tool you
can pick one up on eBay in order for the device to be recognized. I'll be
putting up a tube page dedicated to the kit 2 programming the whole nine
once I speak to Jan about my kit 2 replacement caught on fire lol. Honestly
this company needs to get it together and rework there entire business plan
before selling another product in my opinion they don't have an very good
customer service and  quality control they really need to go back to the
drawing board with the design  honestly just spend the few extra dollars
and buy the multi pro save your self the headaches.  It's alot easier and
doesn't take a programmer to do what it claims it does bottom line the kit
2 is a proof of concept at this stage.

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

najtvis, 2020-02-04:
Hello,

I am sorry for a long delay. I found out, that Arduino released a new version of the Arduino IDE (I used old one) and bootloader which was burned is old type. Please use processor called "**Atmega328p (old bootloader)**" for 3Dsimo KIT2 as well as for 3Dsimo KIT.

I am sorry for troubles with 3Dsimo KIT2
Ondrej Nentvich

fisikos, 2021-01-22:
Hi, received Kit 2 a few days ago and honestly, I am not satisfyed with the 3D pen performance (the main reason I bought it)
- the fillament is going so slow and it makes not nice lines. If I comapre it to the videos , I am even wondering, if this pen will allow to do the bridging.
-
- I was thinking to play with the speed and add some profiles for lower temp (recommended for PLA is 175, wondering why it has 230 by default).
But I am not able to flash the new profiles there (is it enough to add few this lines?).
How about experience with the faster speed? I've added the larger nozzle, so I hope that higher speed will not be a problem there.

The settings are following
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

Closed 2020-02-04.

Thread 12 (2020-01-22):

Parts don't properly fit together

VerscheldeAlynne, 2020-01-22:
I know this is opensource and nothing is ever perfect, but my 3dpen tip is so badly mismatched that it won't extrude filament. I believe this is due to the tube inside being to short and therefor of center.

najtvis, 2020-02-04:
Hi @VerscheldeAlynne,

Could you send us an email to support@3dsimo.com with attached pictures of your troubles? We can help you to solve your difficulties with our product.

hectichead, 2020-04-20:
Same problem here. It's definitely to short and wobbles around loosely inside misaligned. Luckily I have a few mtrs of tube that I bought for my 3d printer, I'm about to cut a longer length and splay the end slightly to make a snug fit, ill let you know how I get on.

hectichead, 2020-05-11:
I used the pen for 15mins and the motor that pulls the filament into the feed has completely packed in. I have emailed 3dsimo a number of times and have had no reply. Not a happy bunny to say the least, this wasn't a cheap buy. I expected far better from these guys.

hectichead, 2020-05-11:
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

didn't help me, I got no reply.

najtvis, 2020-05-12:
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

Hi, when you write to us with a problem? We are replying regularly to everyone in 48 hours. :)

hectichead, 2020-05-12:
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

I've already sent three emails to the email you have provided and the only thing I have received back is an email generated from this site asking me to send another email to the same address stating the problems with photographs. It feels like ground hog day.

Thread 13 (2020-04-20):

3D Pen Design

TechSavage1989, 2020-04-20:

fsvelim1, 2020-04-20:
I asked the same two months ago, the "new" design I received really hides the nozzle, it is impossible to print, you can not see it. I got respond from support, that they really made this change  in last days, but they are planning to release update in next week which will help with this issue. When I downloaded the update from github later on (still the same version), I realized that this is the same version as I recevied, the stupid one. Maybe you will have more luck to convince the designer, that seeing what you are printing is quite important for such a tool :-( This design was made to protect the nozzler from being broken, they had such an issues with the older design, but this is really not a solution. It is like you protect it by covering at all.

TechSavage1989, 2020-04-21:
I ended up just using the foam cutting attachment and cutting of the top portion of the housing and sanding it down clean. The  ceramic tip doesn't have much give without the included support, and I do not see why proper use of the tool would lead to it breaking without the additional support so I'm happy with it now. This was also a good test for the foam cutter, which easily cut through the ABS housing.

redfox05, 2022-01-10:
Was there any update on the design since? I'm considering buying the Simo Kit 2, and struggling to find decent reviews online. Most are for the Pro (none 3d printed one). I figured going for the kit made sense, as I have a 3d printer and can then easily repair if things go wrong. Mainly buying one to fix 3d prints to be honest, and tweak things.

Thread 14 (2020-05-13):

Micro Gear Motor Issues

sbates13, 2020-05-13:
The pen I got worked fine for the first few hours, now the micro gear motor on it seems to be failing. It seems that when trying to pull filament toward the nozzle the gears don’t “catch”, works fine when going in reverse. If I physically move the gears closer together they function properly, but without that they naturally move further apart and the teeth don’t catch on to each other. Is there a way to get a new motor? Or get the gears to stop shifting away from each other?

redfox05, 2022-01-11:
@sbates13 probably way to late for you now, but for anyone else coming across this, this might help? https://www.thingiverse.com/thing:4078267

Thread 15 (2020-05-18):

FW upload not possible - stk500_getsync() error

Demolux, 2020-05-18:
Hi,

I tried to upload the original unmodded Firmware. After a successfull compilation it throws

"avrdude: stk500_getsync() attempt 10 of 10: not in sync: resp=0xe0"
(with attempts 1-9 before of course)

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

Anyone knows what could be wrong?

apphead, 2020-05-21:
> I tried the new bootloader afterwards but it also did not work.
I had the very same issue, but after switching back to new 328P Bootloader, it uploaded FW and started heating. Now display tells me "No tip connected"
So far, experience with this kit is rather frustrating. How about a kit that has FW preloaded or at least a package that includes all libraries. Too much guess work involved and certainly NOT suitable for educational purposes as level of frustration is built-in.

Demolux, 2020-05-21:
> How about a kit that has FW preloaded or at least a package that includes all libraries.

Well mine was already flashed and I have a mostly working pen. However, I want to change the temperatures and speeds and that can only be achieved via FW edit, not on the pen itself. At least this was the case with the currently installed FW when the pen was delivered, maybe the newest FW does allow that - just like the Freemode-Pull-Request.

@apphead Your error rather is rather relying on a poor connection than on the FW I guess. However, you may try the Freemode-FW from AnTi-ArT. I am just a bit confused because it was released in 2018... . Seems like it was for the Kit 1 but Github says there are no conflicts.

Let me know if you try it and if it works.

The poor connection can be improved by getting that mainboard one or two millimeters more to the front. I melted the casing on the two PCB-contact areas with a soldering iron to achieve that.

apphead, 2020-05-22:
I gave up on the pen. Don't like to spend 50 bucks to find out that it is a banana product that ripens at the customers place. Plus, most likely, there is no thermal runaway protection, which basically means the pen could light up in your hands. Given the alpha stage of it.....no thanks.
But thanks for getting back @Demolux and have

bobes74, 2021-03-08:
Hi, I got the same error. I have 3D simo Kit 2. I changed the processor from "ATmega328P" to "ATmega328P (Old Bootloader)" and new firmware updated succesfully.
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

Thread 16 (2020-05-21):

Display says "Not Tip Connected" but Nozzle is heating?

apphead, 2020-05-21:
Flashed latest firmware with EveryTimer-1.1.1 and ssd1306-1.8.2 (as no firmware was pre-loaded?!) and now getting this error.

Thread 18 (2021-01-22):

Unable to flash the new profiles

fisikos, 2021-01-22:
Hi, received Kit 2 a few days ago and honestly, I am not satisfyed with the 3D pen performance (the main reason I bought it)

the fillament is going so slow and it makes not nice lines. If I comapre it to the videos , I am even wondering, if this pen will allow to do the bridging.
I was thinking to play with the speed and add some profiles for lower temp (recommended for PLA is 175, wondering why it has 230 by default).
But I am not able to flash the new profiles there (is it enough to add few this lines?).
How about experience with the faster speed? I've added the larger nozzle, so I hope that higher speed will not be a problem there.
The settings are the following
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

fisikos, 2021-01-26:
hi, so I've figured it out to install ubuntu directly, where the issues with serial port are not appearing (for windows it seems, it require some additional, non-supported by arduino). It would be good to have some update by the developers, as it is not working out-of-the-box for Windows 10.
For the ones, who were not pretty sure about profiles, it is really enough, to add more as you wish with different temp and motor speed.
With a bigger nozzle, you can also increase the motor speed (tested with max of 80%).  I'm also using 175C for PLA without any problem.

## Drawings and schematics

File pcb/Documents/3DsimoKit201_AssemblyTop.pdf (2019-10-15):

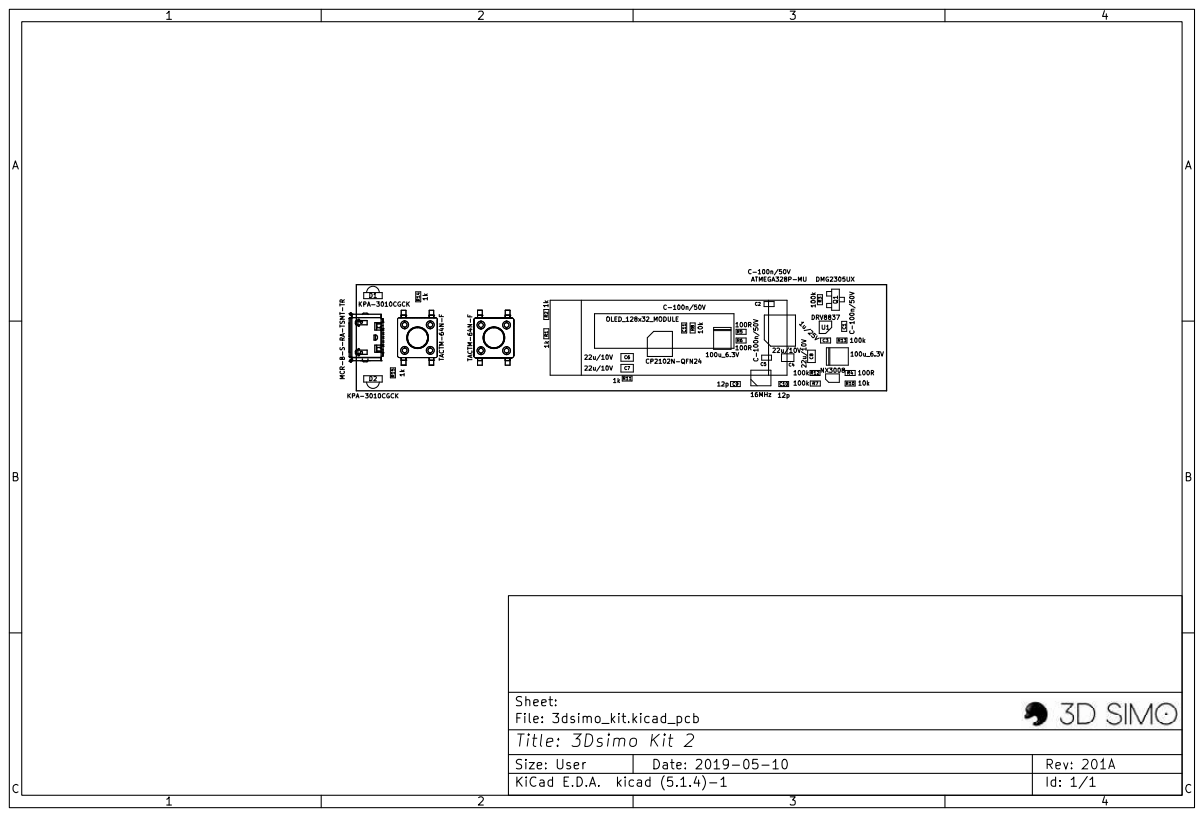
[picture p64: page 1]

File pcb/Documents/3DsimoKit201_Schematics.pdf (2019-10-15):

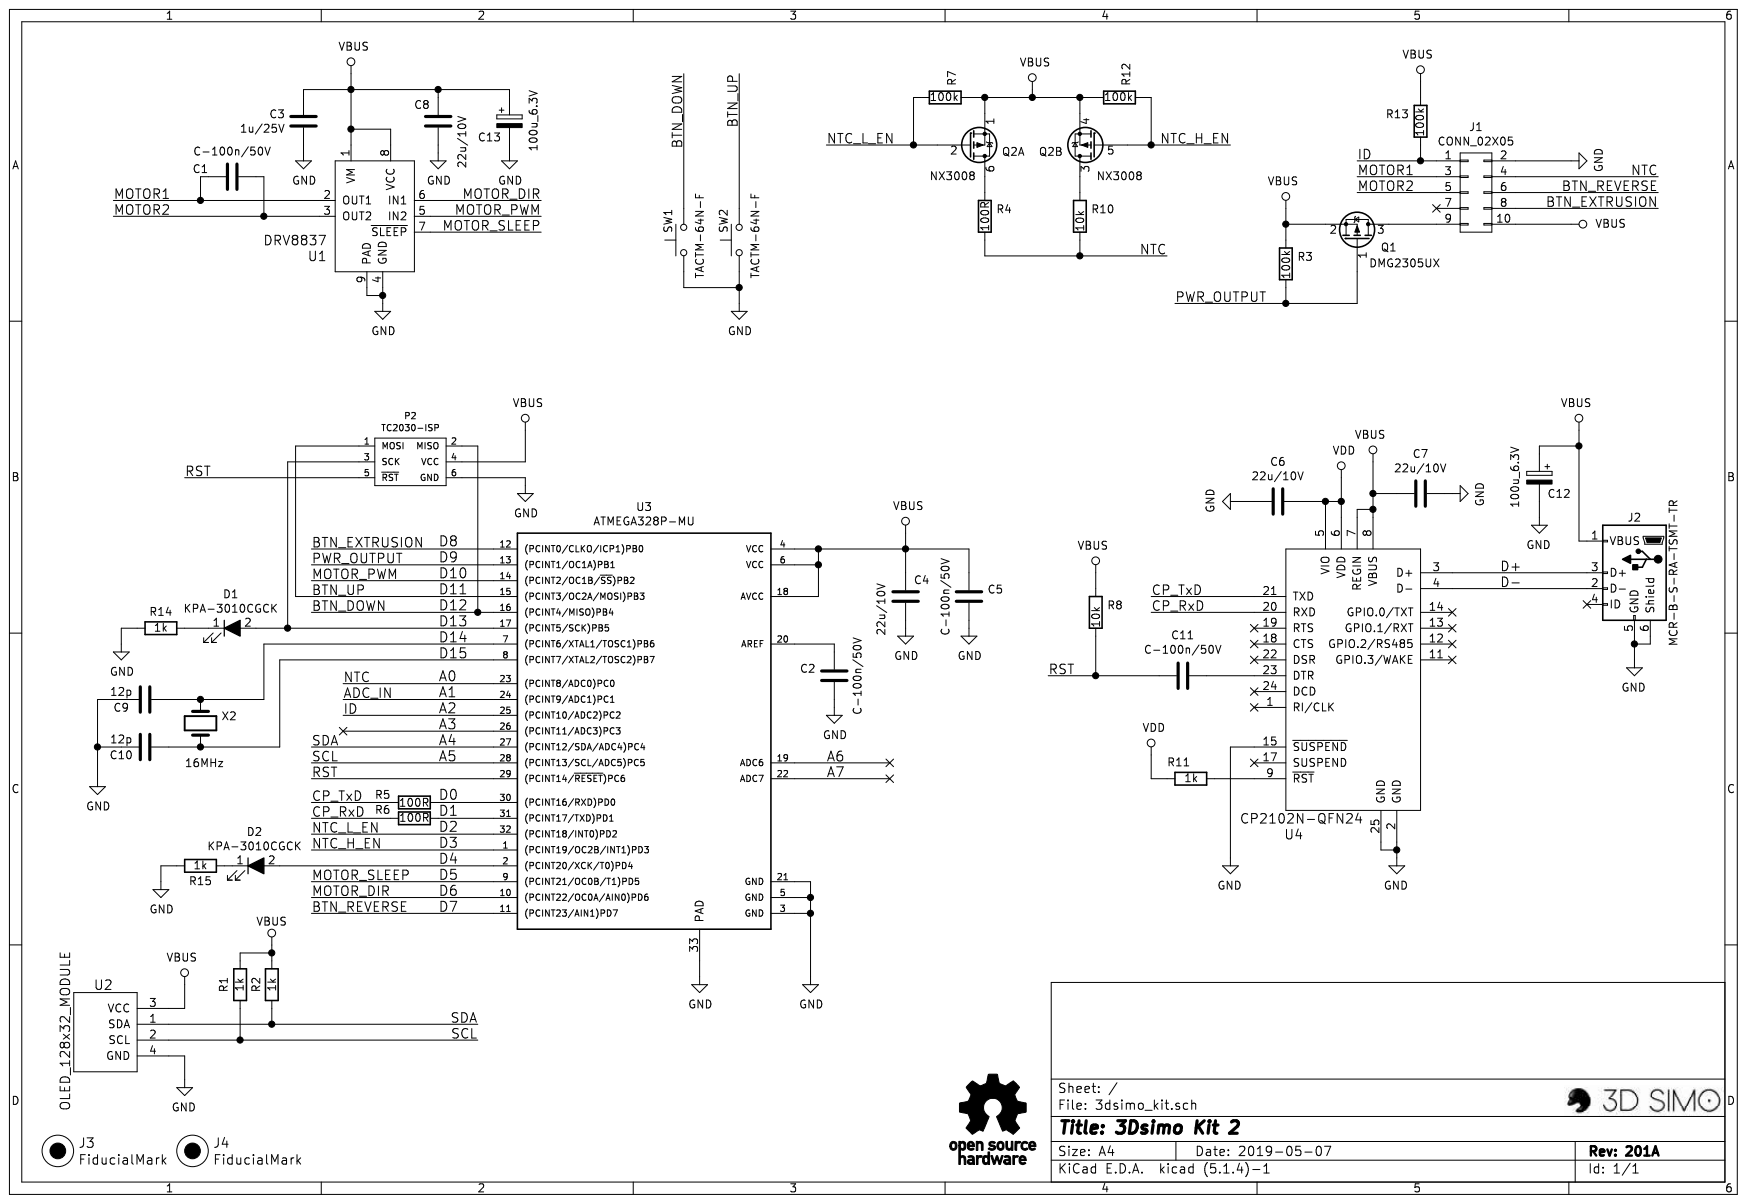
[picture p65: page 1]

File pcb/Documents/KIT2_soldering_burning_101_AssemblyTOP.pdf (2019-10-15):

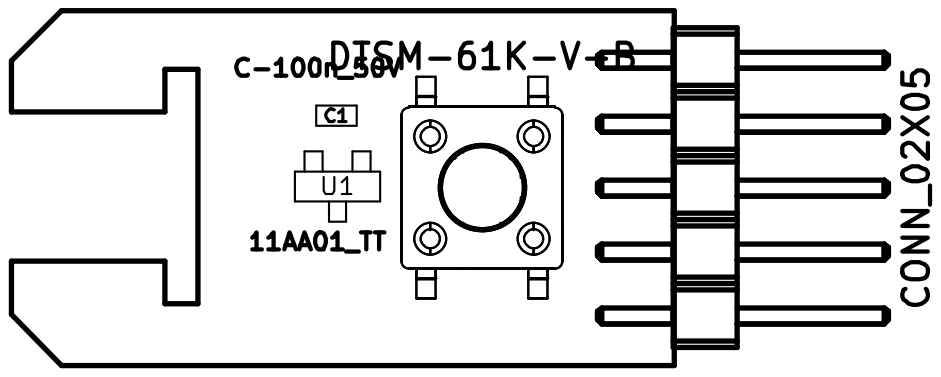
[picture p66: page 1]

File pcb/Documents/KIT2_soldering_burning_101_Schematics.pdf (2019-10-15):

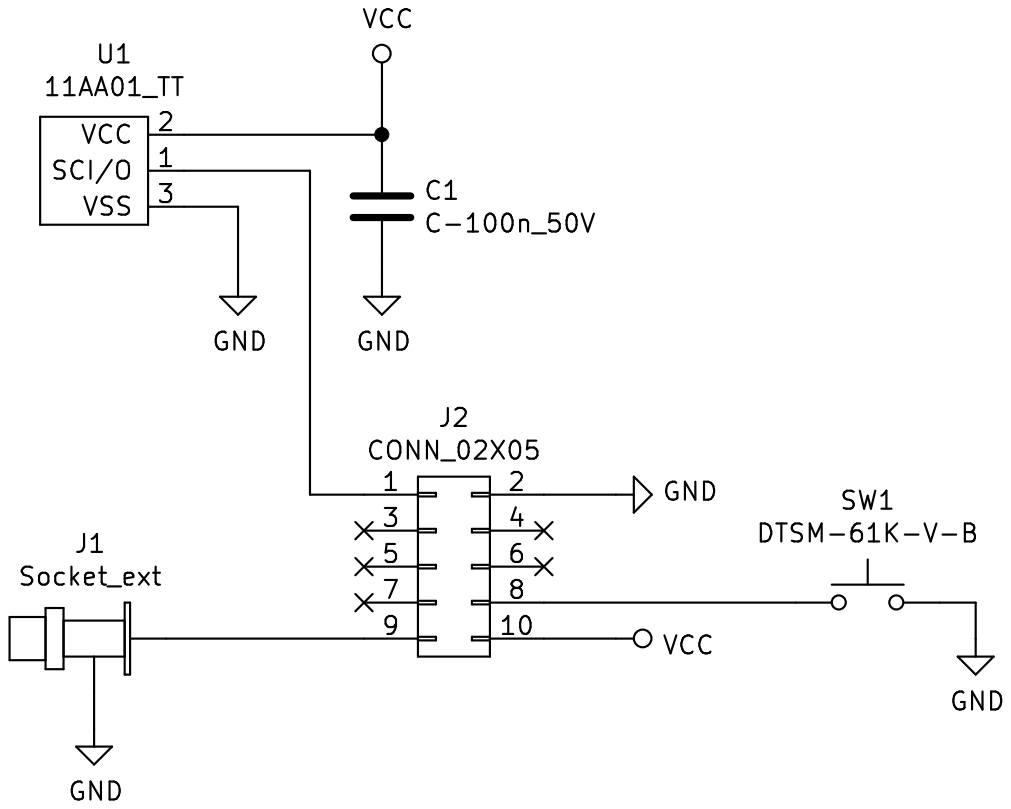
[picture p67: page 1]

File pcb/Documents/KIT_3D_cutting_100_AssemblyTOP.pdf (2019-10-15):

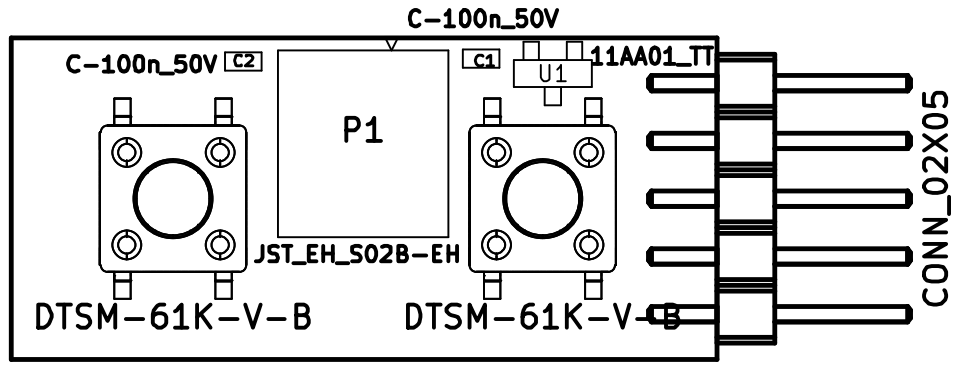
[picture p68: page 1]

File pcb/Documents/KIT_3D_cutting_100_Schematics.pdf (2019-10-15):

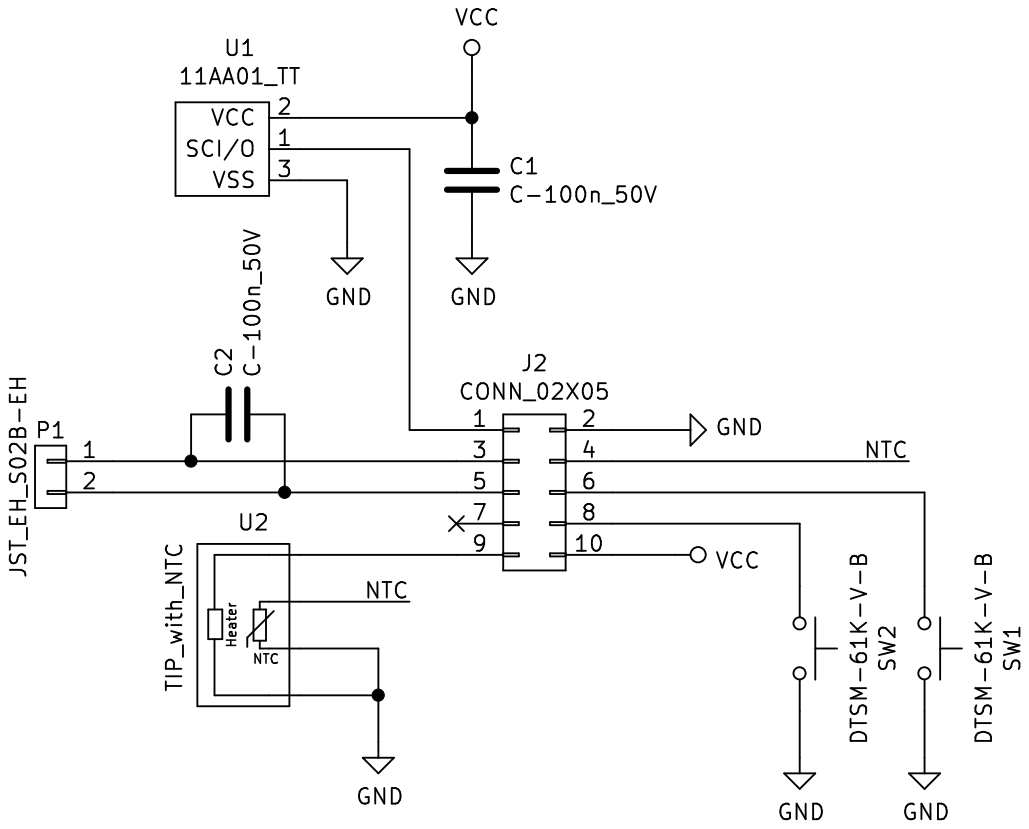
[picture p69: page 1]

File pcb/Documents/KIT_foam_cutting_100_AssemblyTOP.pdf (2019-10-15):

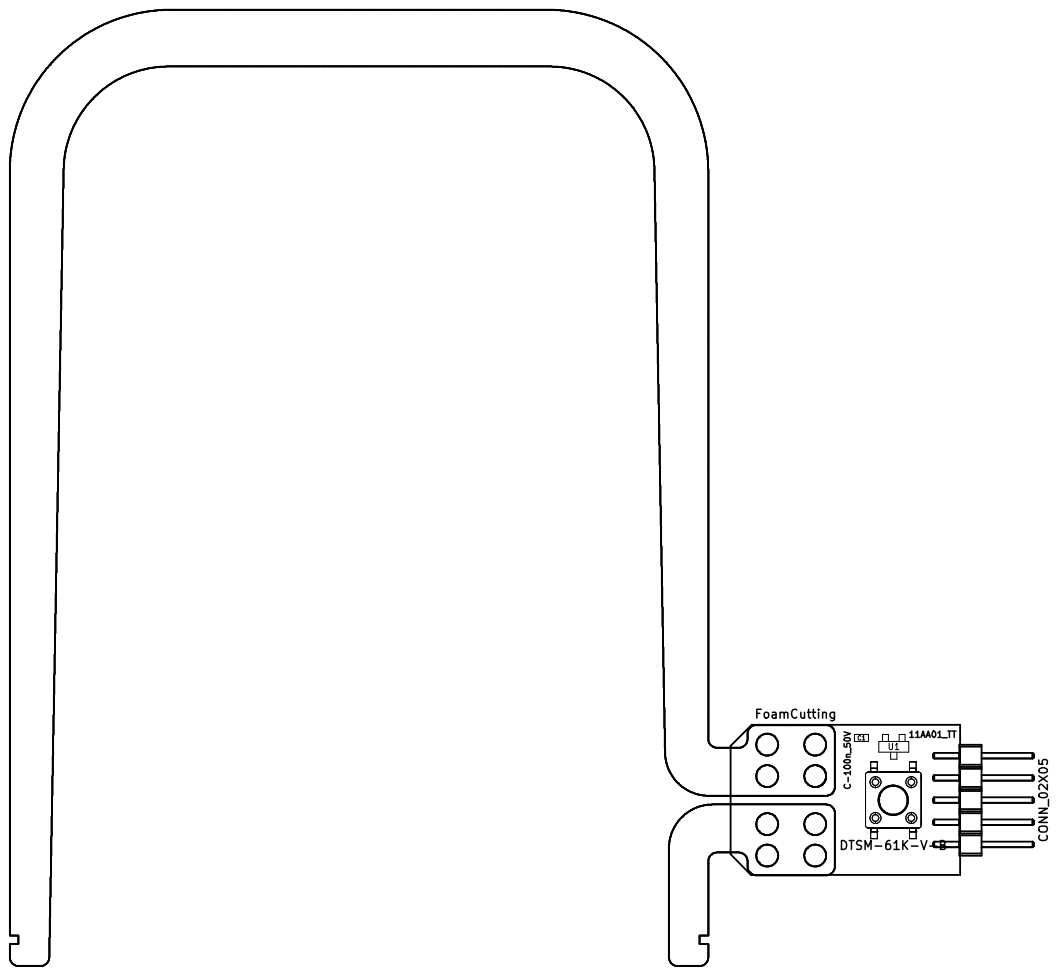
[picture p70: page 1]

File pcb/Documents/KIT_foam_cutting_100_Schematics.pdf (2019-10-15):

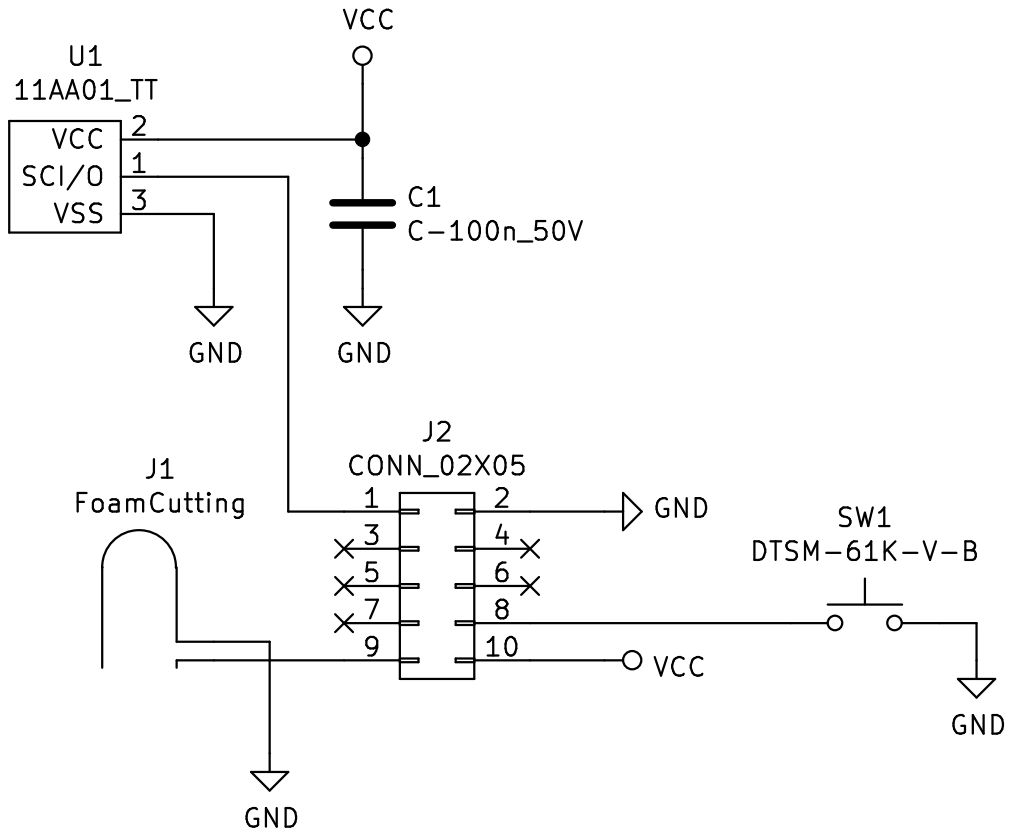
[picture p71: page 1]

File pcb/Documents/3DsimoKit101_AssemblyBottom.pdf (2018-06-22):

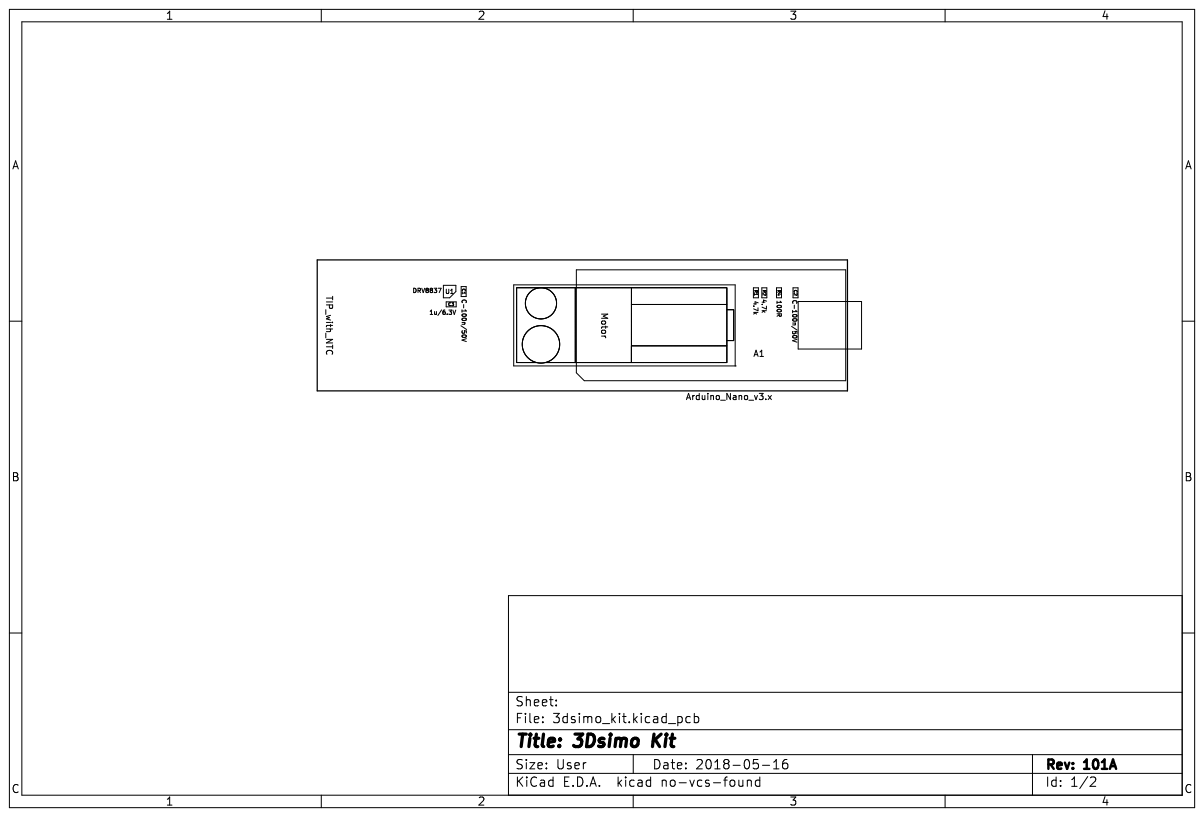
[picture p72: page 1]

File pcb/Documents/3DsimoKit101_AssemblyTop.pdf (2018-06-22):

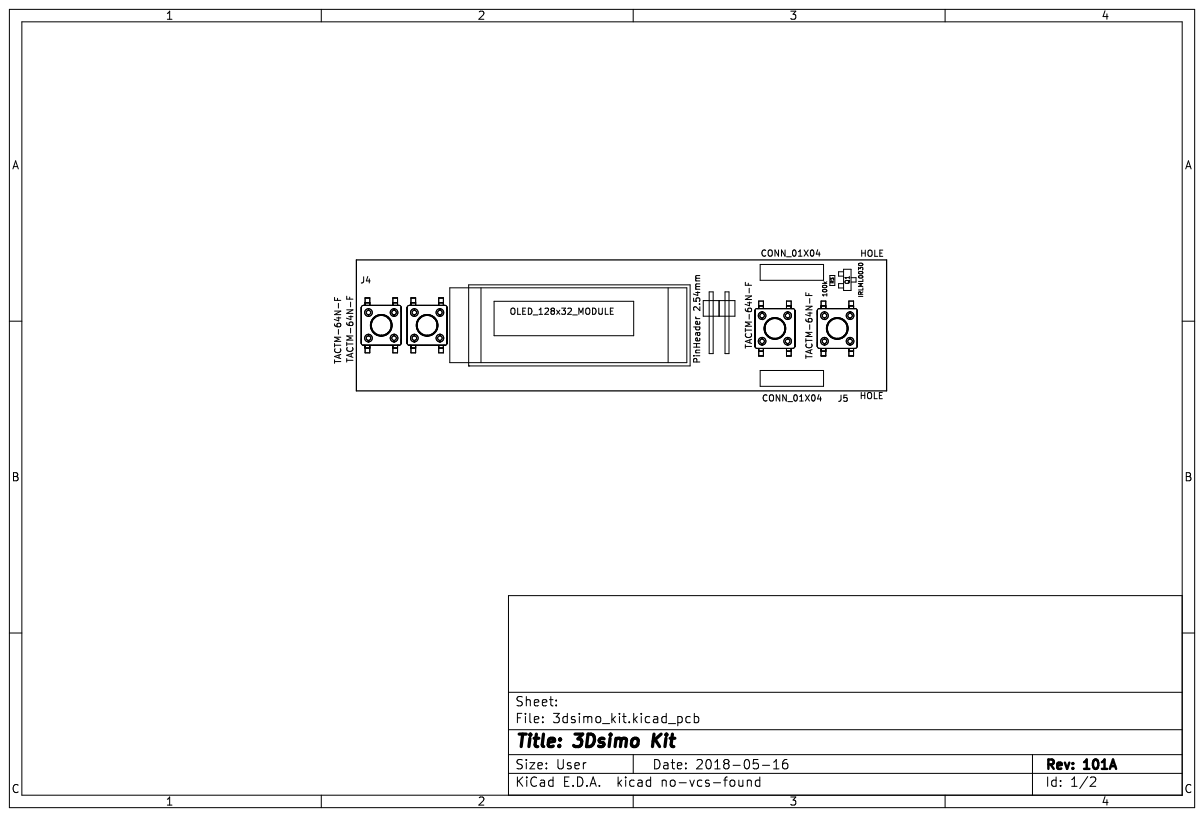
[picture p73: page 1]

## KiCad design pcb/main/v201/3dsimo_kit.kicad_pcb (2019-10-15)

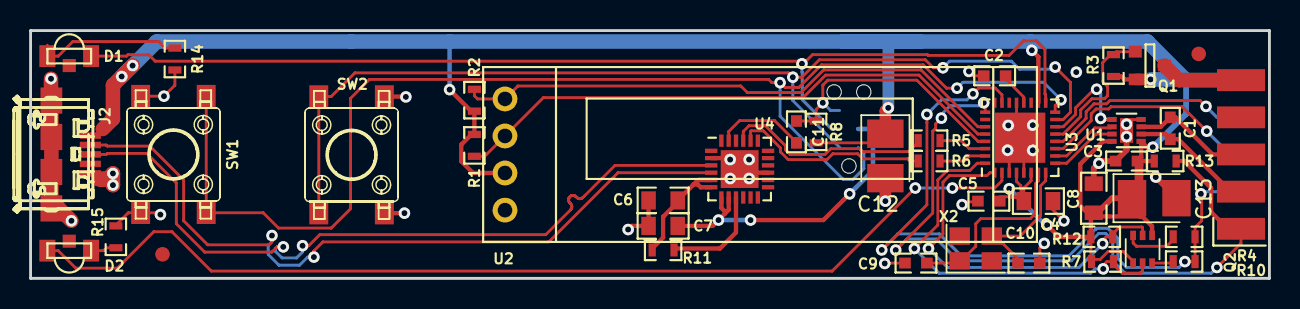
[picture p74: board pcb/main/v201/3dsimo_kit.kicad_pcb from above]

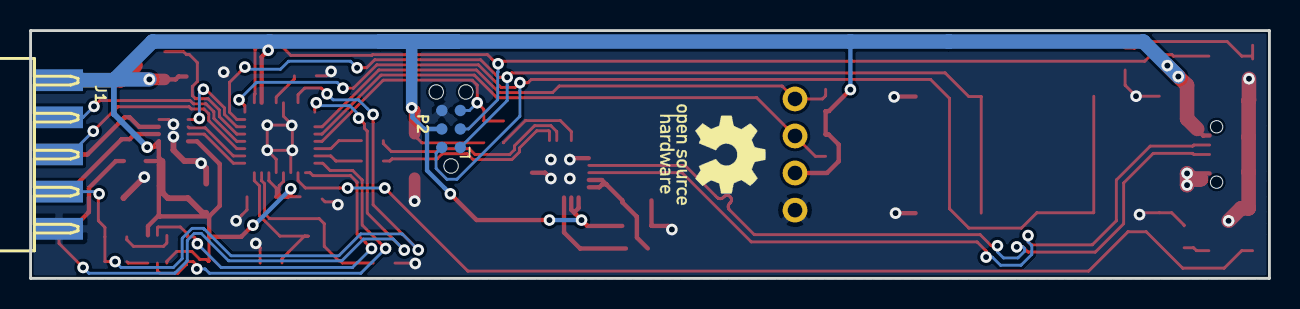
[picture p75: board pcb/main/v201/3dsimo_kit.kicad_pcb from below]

Board: 2 copper layers, 85.0 x 17.0 mm, 44 parts (3 on the bottom side), 38 nets.

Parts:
C1, C2, C5, C11: C-100n/50V; C_0603
C3: 1u/25V; C_0603
C4, C6, C7, C8: 22u/10V; C_0805
C9, C10: 12p; C_0603
C12, C13: 100u_6.3V; CP_Tantalum_Case-B_EIA-3528-21_Reflow
D1, D2: KPA-3010CGCK; KPA-3010
J1: CONN_02X05; Header_for_PCB_edge_2x5_2.54mm
J2: MCR-B-S-RA-TSMT-TR
J3, J4: FiducialMark; AssemblyMark_1.0mm
P2: TC2030-ISP; Tag-Connect_TC2030-IDC-NL
Q1: DMG2305UX; SOT-23
Q2: NX3008; SOT-363_SC-70-6
R1, R2, R11, R14, R15: 1k; R_0603
R3, R7, R12, R13: 100k; R_0603
R4, R5, R6: 100R; R_0603
R8, R10: 10k; R_0603
SW1, SW2: TACTM-64N-F
U1: DRV8837; VDFN-8-1EP_2x2mm_Pitch0.5mm
U2: OLED_128x32_MODULE; OLED_MODULE_128x32_IIC
U3: ATMEGA328P-MU; QFN-32-1EP_5x5mm_Pitch0.5mm
U4: CP2102N-QFN24; QFN-24-1EP_4x4mm_Pitch0.5mm
X1: OSHW; OpenHW_6_9x7_3mm
X2: 16MHz; Crystal_SMD_3225-4pin_3.2x2.5mm

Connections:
/BTN_DOWN: P2.2, SW1.2, U3.16
/BTN_EXTRUSION: J1.8, U3.12
/BTN_REVERSE: J1.6, U3.11
/BTN_UP: P2.1, SW2.2, U3.15
/CP_RxD: R6.2, U4.20
/CP_TxD: R5.1, U4.21
/D+: J2.3, U4.3
/D-: J2.2, U4.4
/ID: J1.1, R13.2, U3.25
/MOTOR1: C1.2, J1.3, U1.2
/MOTOR2: C1.1, J1.5, U1.3
/MOTOR_DIR: U1.6, U3.10
/MOTOR_PWM: U1.5, U3.14
/MOTOR_SLEEP: U1.7, U3.9
/NTC: J1.4, R4.2, R10.2, U3.23
/NTC_H_EN: Q2.5, R12.1, U3.1
/NTC_L_EN: Q2.2, R7.2, U3.32
/PWR_OUTPUT: Q1.1, R3.2, U3.13
/RST: C11.1, P2.5, R8.2, U3.29
/SCL: R1.2, U2.2, U3.28
/SDA: R2.2, U2.1, U3.27
GND: C2.2, C3.2, C4.1, C5.2, C6.1, C7.2, C8.1, C9.2, C10.2, C12.2, C13.2, J1.2, J2.5, J2.6, P2.6, R14.2, R15.2, SW1.1, SW2.1, U1.4, U1.9, U2.4, U3.3, U3.5, U3.21, U3.33, U4.2, U4.15, U4.25
unnamed: C2.1, U3.20
unnamed: C9.1, U3.7, X2.1
unnamed: C10.1, U3.8, X2.3
unnamed: C11.2, U4.23
unnamed: D1.1, R14.1
unnamed: D1.2, P2.3, U3.17
unnamed: D2.1, R15.1
unnamed: D2.2, U3.2
unnamed: J1.9, Q1.3
unnamed: Q2.3, R10.1
unnamed: Q2.6, R4.1
unnamed: R5.2, U3.30
unnamed: R6.1, U3.31
unnamed: R11.1, U4.9
VBUS: C3.1, C4.2, C5.1, C7.1, C8.2, C12.1, C13.1, J1.10, J2.1, P2.4, Q1.2, Q2.1, Q2.4, R1.1, R2.1, R3.1, R7.1, R8.1, R12.2, R13.1, U1.1, U1.8, U2.3, U3.4, U3.6, U3.18, U4.7, U4.8
VDD: C6.2, R11.2, U4.5, U4.6

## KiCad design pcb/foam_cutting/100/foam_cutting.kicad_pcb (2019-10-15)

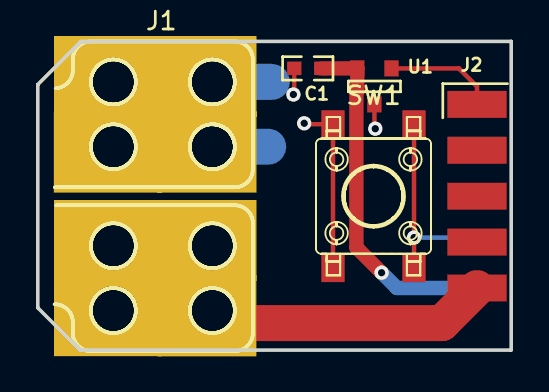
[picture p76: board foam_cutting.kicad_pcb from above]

Board: 2 copper layers, 26.3 x 17.1 mm, 5 parts (0 on the bottom side), 5 nets.

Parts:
C1: C-100n_50V; C_0603
J1: FoamCutting; FoamCutting_110x80mm
J2: CONN_02X05; Header_for_PCB_edge_male_2x5_2.54mm
SW1: DTSM-61K-V-B; SW_SPST_6x6mm_H4.3mm
U1: 11AA01_TT; SOT-23

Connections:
GND: C1.2, J1.1, J2.2, SW1.2, U1.3
unnamed: J1.2, J2.9
unnamed: J2.1, U1.1
unnamed: J2.8, SW1.1
VCC: C1.1, J2.10, U1.2

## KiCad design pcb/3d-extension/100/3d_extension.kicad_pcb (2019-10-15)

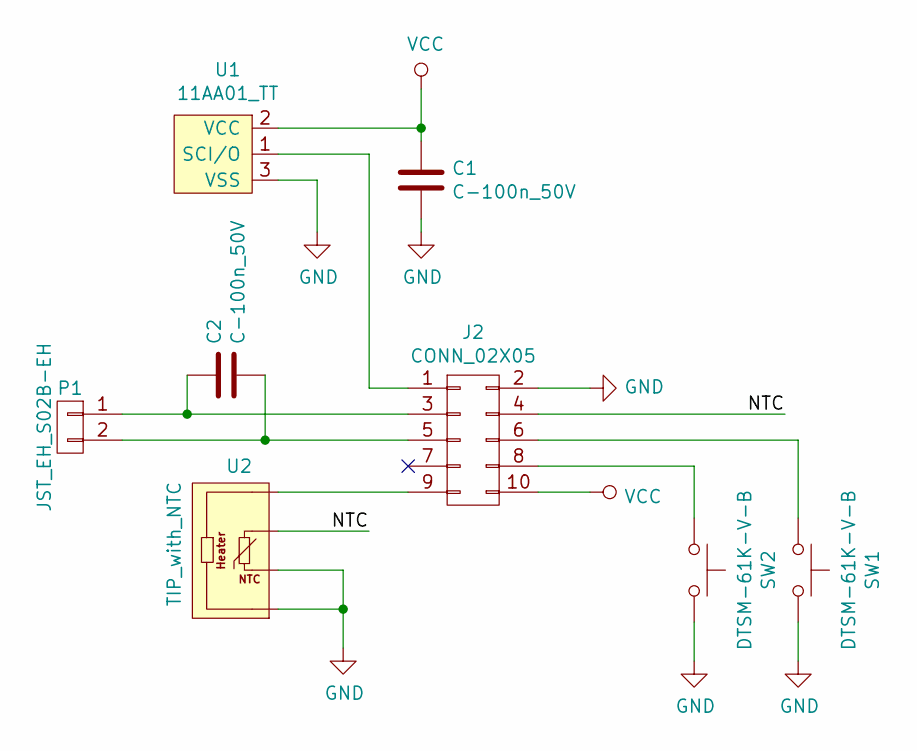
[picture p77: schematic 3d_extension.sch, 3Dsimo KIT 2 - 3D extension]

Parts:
C1, C2: C-100n_50V; C_0603
J2: CONN_02X05; Header_for_PCB_edge_male_2x5_2.54mm
P1: JST_EH_S02B-EH; JST_EH_S02B-EH_02x2.50mm_Angled
SW1, SW2: DTSM-61K-V-B; SW_SPST_6x6mm_H4.3mm
U1: 11AA01_TT; SOT-23
U2: TIP_with_NTC; HOLDER_TIP_NTC_CN

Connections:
/NTC: J2.4, U2.3 (NTC)
GND: C1.2, J2.2, SW1.2, SW2.2, U1.3 (VSS), U2.1 (PWR), U2.2 (NTC)
unnamed: C2.1, J2.3, P1.1
unnamed: C2.2, J2.5, P1.2
unnamed: J2.1, U1.1 (SCI/O)
unnamed: J2.6, SW1.1
unnamed: J2.8, SW2.1
unnamed: J2.9, U2.4 (PWR)
VCC: C1.1, J2.10, U1.2 (VCC)

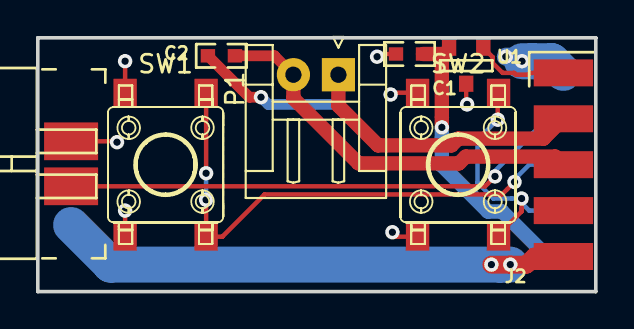
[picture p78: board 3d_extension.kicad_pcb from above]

Board: 2 copper layers, 31.0 x 14.1 mm, 8 parts (1 on the bottom side), 9 nets.

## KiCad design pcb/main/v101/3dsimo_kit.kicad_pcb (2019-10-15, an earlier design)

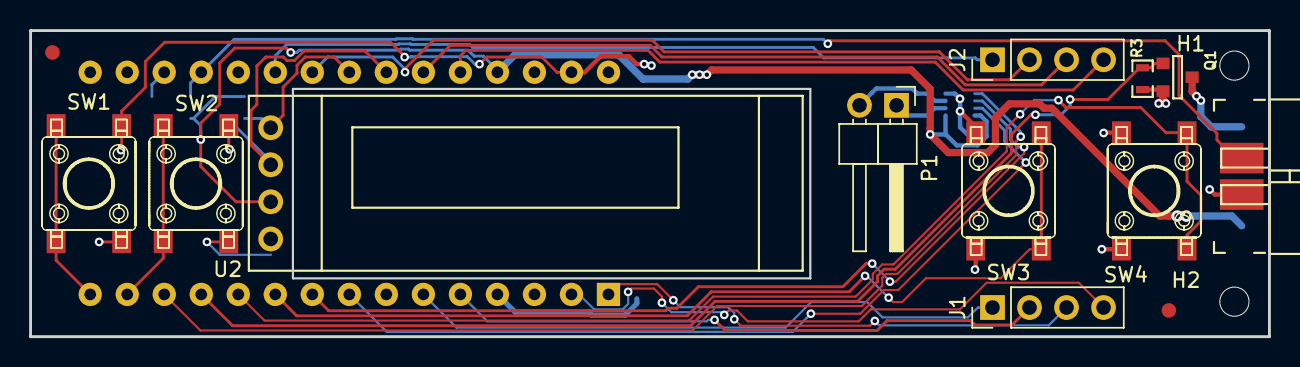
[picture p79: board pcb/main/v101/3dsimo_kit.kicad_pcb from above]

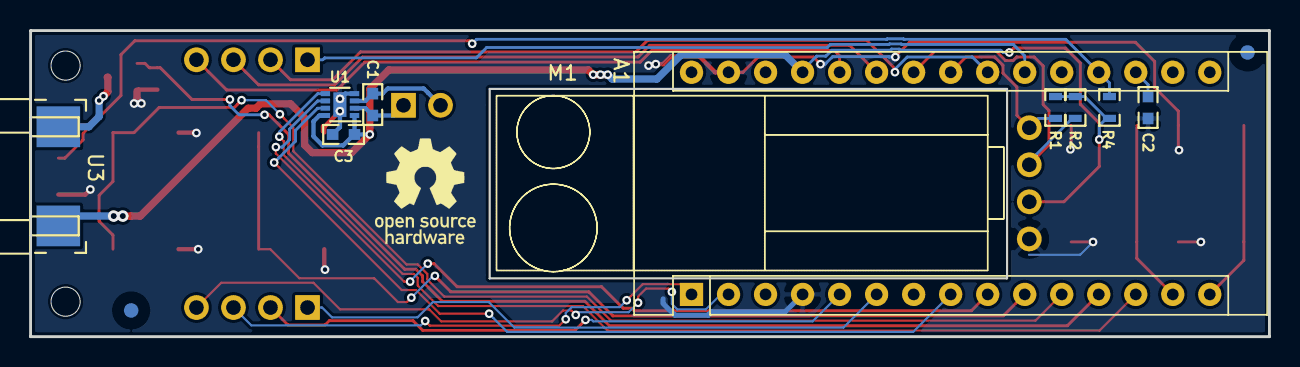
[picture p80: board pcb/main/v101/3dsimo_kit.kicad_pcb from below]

Board: 2 copper layers, 85.0 x 21.0 mm, 27 parts (13 on the bottom side), 25 nets.

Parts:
A1: Arduino_Nano_v3.x; Arduino_Nano
C1, C2: C-100n/50V; C_0603
C3: 1u/6.3V; C_0603
H1, H2: HOLE; MountingHole_2.0mm
J1, J2: CONN_01X04; Pin_Header_Straight_1x04_Pitch2.54mm
J3, J4, J5, J6: FiducialMark; AssemblyMark_1.0mm
M1: Motor; MotorWithTransmission
P1: PinHeader 2.54mm; Pin_Header_Angled_1x02_Pitch2.54mm
Q1: IRLML0030; SOT-23
R1, R2: 4.7k; R_0603
R3: 100k; R_0603
R4: 100R; R_0603
SW1, SW2, SW3, SW4: TACTM-64N-F
U1: DRV8837; VDFN-8-1EP_2x2mm_Pitch0.5mm
U2: OLED_128x32_MODULE; OLED_MODULE_128x32_IIC
U3: TIP_with_NTC; HOLDER_TIP_NTC_CN
X1: OSHW; OpenHW_6_9x7_3mm

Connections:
/BTN_DOWN: A1.15, SW1.2
/BTN_EXTRUSION: A1.11, SW4.2
/BTN_REVERSE: A1.10, SW3.2
/BTN_UP: A1.14, SW2.2
/MOTOR_DIR: A1.9, U1.6
/MOTOR_PWM: A1.13, U1.5
/MOTOR_SLEEP: A1.8, U1.7
/NTC: A1.19, R4.2, U3.3
/PWR_OUTPUT: A1.12, Q1.1, R3.1
GND: A1.4, A1.29, C2.1, C3.2, Q1.2, R3.2, SW1.1, SW2.1, SW3.1, SW4.1, U1.4, U1.9, U2.4, U3.2
unnamed: A1.1, J1.3
unnamed: A1.2, J1.4
unnamed: A1.5, J1.2
unnamed: A1.6, J1.1
unnamed: A1.18, C2.2
unnamed: A1.21, J2.1
unnamed: A1.22, J2.2
unnamed: A1.23, R1.2, U2.1
unnamed: A1.24, R2.2, U2.2
unnamed: A1.25, J2.3
unnamed: A1.26, J2.4
unnamed: C1.1, P1.2, U1.3
unnamed: C1.2, P1.1, U1.2
unnamed: Q1.3, U3.4
VCC: A1.27, C3.1, R1.1, R2.1, R4.1, U1.1, U1.8, U2.3, U3.1

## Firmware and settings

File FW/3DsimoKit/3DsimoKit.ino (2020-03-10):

/*
 *  ssd1306   128x32   Alexey Dinda Library
 */
#include "ssd1306.h"
#include "nano_gfx.h"
#include <EveryTimer.h>

/*
 *   define Input/Outputs
 */

#define LED_NANO    13    // LED placed on Arduino Nano board

#define BTN_UP      12    // controlling button UP/PLUS                /* NEW! changed for right hand - default 11 */
#define BTN_DOWN    11    // controlling button DOWN/MINUS             /* NEW! changed for right hand - default 12 */
#define BTN_EXT     8     // button for material extrusion
#define BTN_REV     7     // button for material reverse

#define MOTOR_DIR   6     // motor direction output
#define MOTOR_PWM   10    // motor PWM output for power driving
#define MOTOR_SLEEP 5
#define HEATER_EN   9     // heater/power output 

#define TEMP_IN     A0    // temperature measure ADC input 

/*
 *   define heating states
 */
enum {
  STATE_HEATING,
  STATE_COOLING,
  STATE_READY,
} STATE_e;

enum {
  MOTOR_STOP,
  MOTOR_EXTRUSION,
  MOTOR_REVERSE,
  MOTOR_CONTINUOUS,
  MOTOR_REVERSE_AFTER_EXTRUSION
} MOTOR_STATE_e;

/*
 *   define structure for the material list
 */
typedef struct {
  int temperature;
  int motorSpeed;
  char* materialName;
} profile_t;

/*
 *   define material profiles
 */
const profile_t materials[] PROGMEM = {  
  // {temperature (deg. C), motorSpeed (%), materialName}
     {0,                  0,             "OFF"},    /* NEW! BEGIN OFF - BUT IF YOU SELECT THIS AFTER PETG, 3DPEN COOLS TO 153º PRIOR TO SHUTDOWN*/
     {210,                  40,             "PLA"},
     {235,                  40,             "ABS"},
     {235,                  40,             "PETG"}
};

/*
 *   define number of materials in list and variables
 */
#define MATERIAL_COUNT  4

int materialID = 0;         // chosen material profile
int setTemperature = 210;   // set heater temperature
int setMotorSpeed = 60;     // set motor speed in %

/*
 *   create timer for main loop
 */
EveryTimer timer;

/*
 *   function for measuring temperature of the tip
 */
int getTemperature(){  // get temperature in deg. Celsius from ADU value
  // set reference for ADC to power supply (5V)
  analogReference(DEFAULT);

  int avgTemp = 0;
  for(int i = 0; i<16; i++){
    avgTemp += analogRead(TEMP_IN);
  }
  
  // read averaged analog value of temperature
  long tempADU = avgTemp >> 4;
  
  // convert ADU into temperature
  // constants could slightly change for different ceramic tip
  tempADU -= 1692; // increase this value when temperature is too high and vice versa
  tempADU <<= 7;
  tempADU /= (-557); 
  
  return tempADU; 
}

/*
 *   load actual material profile
 */
void loadMaterial(int id){
  profile_t profile;
  char text[10];
  
  // load material profile from PROGMEM and assign variables
  memcpy_P(&profile, &materials[id], sizeof(profile_t));
  setTemperature = profile.temperature;
  setMotorSpeed  = profile.motorSpeed;
  
  // clear display and show all information
  sprintf(text, "%d %%", setMotorSpeed);
  ssd1306_clearScreen();
  ssd1306_setFixedFont(ssd1306xled_font6x8);
  ssd1306_printFixedN(0,  0, profile.materialName, STYLE_NORMAL, FONT_SIZE_2X);  
  ssd1306_printFixedN(80, 0, text, STYLE_NORMAL, FONT_SIZE_2X);
}

/*
 *  PID variables and constants for tuning
 */
float Kp=15, Ki=1, Kd=1.0, dT = 0.1, Hz=10;

/*
 *   basic PID routine to get output value
 */
int getPIDoutput(int setPoint, int actualValue, int maxValue, int minValue){
  static float sumE = 0;
  static int16_t error, previousError = 0;
  float outputValue;
  static int pidAvg[4] = {0,0,0,0};
  static int pidAvgIndex = 0;
  

  // reset sumE when actualValue exceed setPoint by 5
  static int noWaitCycles = 0;
  if(actualValue > setPoint + 5){
    ++noWaitCycles;
    if(noWaitCycles >= 30){
      sumE = 100;
      noWaitCycles = 0;
    }
  }
  else{
    noWaitCycles = 0;
  }

  // PID implementation
  error = setPoint - actualValue;
  sumE += (float) error * dT;
  outputValue =  Kp*error + Ki*sumE + Kd*(error - previousError)/dT;
  previousError = error;

  // restrict output PID value into range between minValue and maxValue
  if(outputValue > maxValue)
    outputValue = maxValue;
  else if(outputValue < minValue)
    outputValue = minValue;

  // store n output values for averaging
  pidAvg[pidAvgIndex] = outputValue;
  ++pidAvgIndex;
  if(pidAvgIndex >= 4)
    pidAvgIndex = 0;

  // average last n output values
  int sumPIDavg = 0;
  for(int i = 0; i<4; i++){
    sumPIDavg += pidAvg[i];
  }
  sumPIDavg >>= 2;
  
  return sumPIDavg;
}

#define NO_AVERAGES_VALUES  64

/*
 *   heating function for heater driving by PID regulator
 */
int heating(){
  static int tempAvg[NO_AVERAGES_VALUES];   // temperature array for averaging it
  static int tempAvgIter = 0;               // current index in temperature array
  static char firstTime = 0;                // if is 1, this function ran at least one time
  char text[30];                            // buffer for text

  // variables initialization
  if(!firstTime){
    memset(tempAvg, 0, sizeof(tempAvg)*sizeof(int));
    firstTime = 1;
  }

  // resolve PID value for heater PWM
  int temperature = getTemperature();
  int valuePID = getPIDoutput(setTemperature, temperature, 255, 0);
   
  analogWrite(HEATER_EN, valuePID);

  // save actual temperature for averaging
  tempAvg[tempAvgIter] = temperature;
  if(++tempAvgIter>=NO_AVERAGES_VALUES)
    tempAvgIter = 0;

  // make temperature average from NO_AVERAGES_VALUES
  int sumTemp = 0;
  for(int i = 0; i<NO_AVERAGES_VALUES; i++){
    sumTemp += tempAvg[i];  
  }
  sumTemp /= NO_AVERAGES_VALUES;

  // show on display actual and preset temperature
  sprintf(text, "%3d/%3dC", sumTemp, setTemperature);
  ssd1306_setFixedFont(ssd1306xled_font6x8);
  ssd1306_printFixedN(0, 16, text, STYLE_NORMAL, FONT_SIZE_2X);

/*
 * debug output into display and to serial
 */
/*
  sprintf(text, "PID=%03d", valuePID);
  ssd1306_printFixed(0, 0, text, STYLE_NORMAL);

  sprintf(text, "%3d;%3d", valuePID, sumTemp);
  Serial.println(text);
*/
  
  return sumTemp;
}

/*
 *   call every 50ms timer for buttons action and heating 
 *   execute buttons function according to heating state
 *   change material profile   
 */
void timerAction(){
  static int elapsedTime = 0;
  static char statusHeating = STATE_HEATING;   
  static char stateMotor = MOTOR_STOP, lastMotorState = MOTOR_STOP;
  static int timeMotorReverse = 0;

  // decide temperature state (heating, cooling, ready) and show it on display
  if(++elapsedTime==2){ // 100ms
    elapsedTime = 0;
    int actualTemperature = heating();
    
    // tolerant zone where temperature is ABOVE preset temperature, 
    // but it is possible to do extrusion/reverse
    if(actualTemperature > setTemperature + 10){
      statusHeating = STATE_COOLING;
      ssd1306_printFixedN(116, 16, "C", STYLE_NORMAL, FONT_SIZE_2X);
    }

    // tolerant zone where temperature is OK for extrusion/reverse
    else if(actualTemperature > setTemperature - 10){
      statusHeating = STATE_READY;
      ssd1306_printFixedN(116, 16, "R", STYLE_NORMAL, FONT_SIZE_2X);
      digitalWrite(LED_NANO, HIGH);   // turn the LED on (HIGH is the voltage level)
    }

    // tolerant zone where temperature is LOW for extrusion/reverse
    else{
      statusHeating = STATE_HEATING;
      ssd1306_printFixedN(116, 16, "H", STYLE_NORMAL, FONT_SIZE_2X);
      digitalWrite(LED_NANO, !digitalRead(LED_NANO));   // turn the LED on (HIGH is the voltage level)
    }
  }

  // assing functions according to heating state (mainly button function)
  switch(statusHeating){
    case STATE_COOLING:
    case STATE_READY:{
      // button EXTRUSION is pressed, extrude material
      if(!digitalRead(BTN_EXT) && digitalRead(BTN_REV)){
        stateMotor = MOTOR_EXTRUSION;
      }
      
      // button REVERSE is pressed, retract material
      else if(digitalRead(BTN_EXT) && !digitalRead(BTN_REV)){
        stateMotor = MOTOR_REVERSE;
        timeMotorReverse = 400; // reverse time is 50ms * timeMotorReverse (400 = 20s)
      }
      
      // both buttons are pressed, motor stopped
      else if(!digitalRead(BTN_EXT) && !digitalRead(BTN_REV)){
        stateMotor = MOTOR_STOP;
      }
      
      // not buttons are pressed
      else{
        if(lastMotorState == MOTOR_EXTRUSION){
          stateMotor = MOTOR_REVERSE_AFTER_EXTRUSION;
          timeMotorReverse = 20; // reverse time is 50ms * timeMotorReverse (20 = 1s)
        }
      }    
      break;
    }
    
    case STATE_HEATING:
      // if happened that heater has so low temperature, motor stop
      digitalWrite(MOTOR_DIR, LOW);
      analogWrite(MOTOR_PWM, 0);
      stateMotor = MOTOR_STOP;
      break;
  }

  // resolve motor states (Extrusion, Reverse, Stop, ...)
  switch(stateMotor){
    case MOTOR_STOP:
      digitalWrite(MOTOR_DIR, LOW);
      analogWrite(MOTOR_PWM, 0);
      break;
      
    case MOTOR_EXTRUSION:{
      int pwmSpeed = setMotorSpeed*255;
      digitalWrite(MOTOR_DIR, LOW);
      analogWrite(MOTOR_PWM, pwmSpeed/100);
      break;
    }
    
    case MOTOR_REVERSE:
      --timeMotorReverse;
      if(timeMotorReverse > 0){
        digitalWrite(MOTOR_DIR, HIGH);
        analogWrite(MOTOR_PWM, 0);
      }
      else{
        stateMotor = MOTOR_STOP;
      }
      break;

    case MOTOR_REVERSE_AFTER_EXTRUSION:
      --timeMotorReverse;
      if(timeMotorReverse > 0){
        int pwmSpeed = (100-setMotorSpeed)*255;
        digitalWrite(MOTOR_DIR, HIGH);
        analogWrite(MOTOR_PWM, pwmSpeed/100);
      }
      else{
        stateMotor = MOTOR_STOP;
      }  
      break;        
  }
  lastMotorState = stateMotor;  
  
  // one time action, mainly for material change
  static char buttonsPressed = 0;



// button UP pressed
  if(!digitalRead(BTN_UP) && digitalRead(BTN_DOWN)){
    if(!(buttonsPressed & 0x01)){
      if(materialID < MATERIAL_COUNT-1){
        ++materialID;        
      }
      else{
        materialID = 0;
      }
      loadMaterial(materialID);
    }
    // save that this button UP was already pressed and used
    buttonsPressed |= 0x01;
  }
  else{
    // save that this button UP was released
    buttonsPressed &= 0xFE;
  }

  // button DOWN pressed
  if(digitalRead(BTN_UP) && !digitalRead(BTN_DOWN)){
    if(!(buttonsPressed & 0x02)){
      if(materialID > 0){
        --materialID;
      }
      else{
        materialID = MATERIAL_COUNT-1;
      }
      loadMaterial(materialID);
    }
    // save that this button DOWN was already pressed and used
    buttonsPressed |= 0x02;
  }
  else{
    // save that this button DOWN was released
    buttonsPressed &= 0xFD;
  }
  
}

/*
 *   GPIO, OLED initialize
 *   load material profile
 *   preset timer
 */
void setup() {

  // initialize OLED display
  ssd1306_128x32_i2c_init();
  ssd1306_clearScreen();
  ssd1306_flipHorizontal(1);  /* oled_ssd1306.h   NEW! rotate screen in X */
  ssd1306_flipVertical(1);   /* oled_ssd1306.h   NEW!  rotate screen in Y */
  

  // initialize outputs 
  pinMode(LED_NANO,  OUTPUT);
  pinMode(MOTOR_DIR, OUTPUT);
  pinMode(MOTOR_PWM, OUTPUT);
  pinMode(MOTOR_SLEEP, OUTPUT);
  pinMode(HEATER_EN, OUTPUT);

  // initialize inputs
  pinMode(BTN_UP,   INPUT_PULLUP);
  pinMode(BTN_DOWN, INPUT_PULLUP);
  pinMode(BTN_EXT,  INPUT_PULLUP);
  pinMode(BTN_REV,  INPUT_PULLUP);

  // load material profile
  loadMaterial(materialID);

  // preset timer period every 50 ms and call timerAction function when time expire
  timer.Every(50, timerAction);

  // initialize outputs
  digitalWrite(MOTOR_SLEEP, HIGH);

  Serial.begin(9600);
}

/*
 *   main loop
 */
void loop() {
  // call timer each preset period
  timer.Update();
}

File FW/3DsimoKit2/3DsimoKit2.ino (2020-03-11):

/*
 *  ssd1306   128x32   Alexey Dinda Library
 */
#include <stdio.h>
#include <string.h>
#include "config.h"
#include "ssd1306.h"
#include "nano_gfx.h"
#include "nanodeUNIO.h"
#include "accessories.h"
#include <EveryTimer.h>

/*
 *   create timer for main loop 
 */
EveryTimer timer;

bool righthanded = true;
bool pressUPDOWNhandled = true;
extern int materialID;

/*
 *   call every 50ms timer for buttons action and heating 
 *   execute buttons function according to heating state
 *   change material profile   
 */
void timerAction(){
  accessories_t acs;
  static accessories_t acsLast;
  char text[20];

  acsIdentify();
  acs = getAccessories();  
  
  if(acsLast.type != acs.type){
    ssd1306_clearScreen();    
  }
  
  if(acs.type == ACS_NONE){
    sprintf(text, "No tip     ");
    ssd1306_setFixedFont(ssd1306xled_font6x8);
    ssd1306_printFixedN(0, 0, text, STYLE_NORMAL, FONT_SIZE_2X);
    
    sprintf(text, "Connected  ");
    ssd1306_setFixedFont(ssd1306xled_font6x8);
    ssd1306_printFixedN(0, 16, text, STYLE_NORMAL, FONT_SIZE_2X);
  }
  else {
    acs.function();    
  }
  if(acs.type != acsLast.type){
      acs.startup();
    }
  acsLast = acs;

  // button UP & DOWN pressed: change display 
  if(!digitalRead(BTN_UP) && !digitalRead(BTN_DOWN) ){
    if (! pressUPDOWNhandled) {
      righthanded = ! righthanded;
      pressUPDOWNhandled = true;

      ssd1306_clearScreen();
      if (righthanded) {
        ssd1306_flipHorizontal(1);  /* rotate screen in X */
        ssd1306_flipVertical(1);    /* rotate screen in Y */
      } else {
        ssd1306_flipHorizontal(0); 
        ssd1306_flipVertical(0); 
      }
    }
  }
  else{
    pressUPDOWNhandled = false;
  }
}

/*
 *   GPIO, OLED initialize
 *   load material profile
 *   preset timer
 */
void setup() {

  // initialize OLED display
  ssd1306_128x32_i2c_init();
  ssd1306_clearScreen();
  ssd1306_flipHorizontal(1);  /* oled_ssd1306.h   NEW! rotate screen in X */
  ssd1306_flipVertical(1);   /* oled_ssd1306.h   NEW!  rotate screen in Y */
  
  

  // initialize outputs 
  digitalWrite(HEATER_EN, HIGH);
  digitalWrite(HIGH_TEMP_EN, LOW);
  digitalWrite(LOW_TEMP_EN, HIGH);
  
  pinMode(LED_R,  OUTPUT);
  pinMode(LED_L,  OUTPUT);
  pinMode(MOTOR_DIR, OUTPUT);
  pinMode(MOTOR_PWM, OUTPUT);
  pinMode(MOTOR_SLEEP, OUTPUT);
  pinMode(HEATER_EN, OUTPUT);
  pinMode(HIGH_TEMP_EN, OUTPUT);
  pinMode(LOW_TEMP_EN, OUTPUT);

  // initialize inputs
  pinMode(BTN_UP,   INPUT_PULLUP);
  pinMode(BTN_DOWN, INPUT_PULLUP);
  pinMode(BTN_EXT,  INPUT_PULLUP);
  pinMode(BTN_REV,  INPUT_PULLUP);

  // preset timer period every 50 ms and call timerAction function when time expire
  timer.Every(50, timerAction);

  // initialize outputs
  digitalWrite(MOTOR_SLEEP, HIGH);

  Serial.begin(9600);
}

/*
 *   main loop
 */
void loop() {
  // call timer each preset period
  timer.Update();

  if (Serial.available() > 0) {
    char incomingByte;
    // read the incoming byte:
    incomingByte = Serial.read();
    Serial.write(incomingByte);
  }
}

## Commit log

2018-06-22 added 3D models of housing
    [Back_Top.stl, Central_Bottom.stl, Central_Top.stl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]
2018-12-21 added 3d models (STL, STP)
    [Back_Top.stl, Back_top.stp, Central_Bottom.stl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]
2019-10-15 updated v101, added pcb and FW for KIT 2
    [3d_extension.kicad_pcb, 3d_extension.sch, 3dsimo_kit.kicad_pcb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]
2019-10-15 updated documentation
    [3DDRAW_L.stl, 3DDRAW_R.stl, BURNING_SOLDERING_L.stl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]
2019-11-29 added stp model and manual
    [3DDRAW_L.stp, 3DDRAW_R.stp, BURNING_SOLDERING_L.stp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]
2019-12-10 LEDs turn off when cooling
2020-02-21 added screen flip, improved PID controller
    [3DsimoKit2.ino, accessories.c]
2020-03-10 updated 3D parts
    [3D LEFT.stl, 3D RIGHT.stl, 3DDRAW_L.stl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]
2020-03-11 updated profiles and minor bugfixes
    [3DsimoKit2.ino, accessories.c]
2020-03-12 updated parts locations in sch
    [3dsimo_kit.sch]
2020-04-21 Add files via upload
    Added newer 3D models for KIT2
    [3D LEFT.stl, 3D RIGHT.stl, 3D_DRAW_L.step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]
2020-08-04 Change name of Single button ring
    [SINGLE BUTTON RING.stl]
2020-09-29 Add files via upload
    Battery_adaptor_stl_files_added
    [BAT_LEFT.stl, BAT_LEFT_SUPPORTS.stl, BAT_PCB_HOLDER.stl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]
